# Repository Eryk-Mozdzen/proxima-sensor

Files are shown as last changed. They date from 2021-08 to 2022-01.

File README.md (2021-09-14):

# "Proxima" sensor

Simple, low cost, IR proximity sensor, designed for minisumo class robots. Operates at 56 kHz frequency. Dimensions: 12x17x15 mm.

## Projects goals
- \>20cm detection range
- 3.3/5V power supply voltage
- \<100mA power supply current
- single logic output
- smallest possible dimensions
- not operating at 38 kHz ([robot start module](https://p1r.se/startmodule/) frequency)
- plastic case
- status led

## Workflow

### Done:
- version 1.0 assembly
- raw tests
- replace resistors to compensate parasitic capacity
- tests with case

### In progress:
- searching for new square wave generator (NE555 is not suitable for aplications below 4.5V, but works)
- design better case 
	* receiver closer to front
	* add wall between receiver and transmitter led
	* add gap to improve taking out elektronics
	* increase hole diameter

### To do:
- print & test improved case

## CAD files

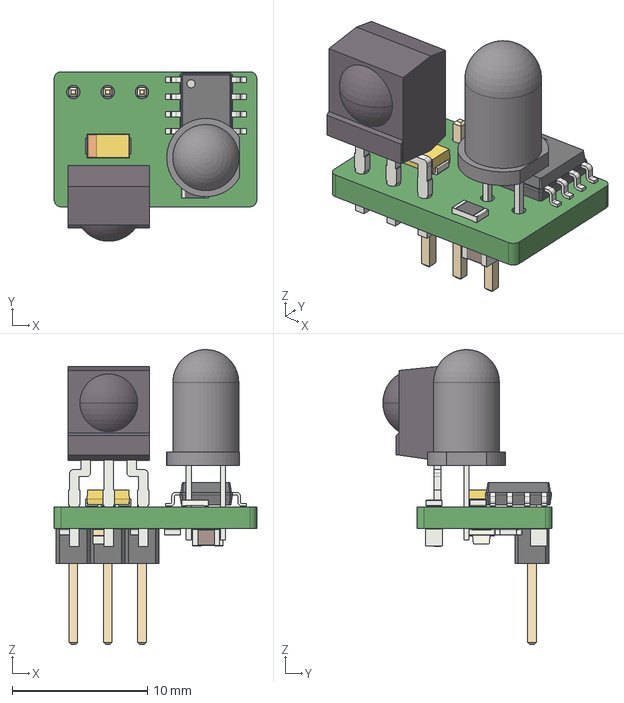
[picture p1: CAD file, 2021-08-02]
version_1.xx/proxima_sensor_case/exported_from_kicad/proxima_sensor_board.step
15.0 x 12.5 x 21.8 mm

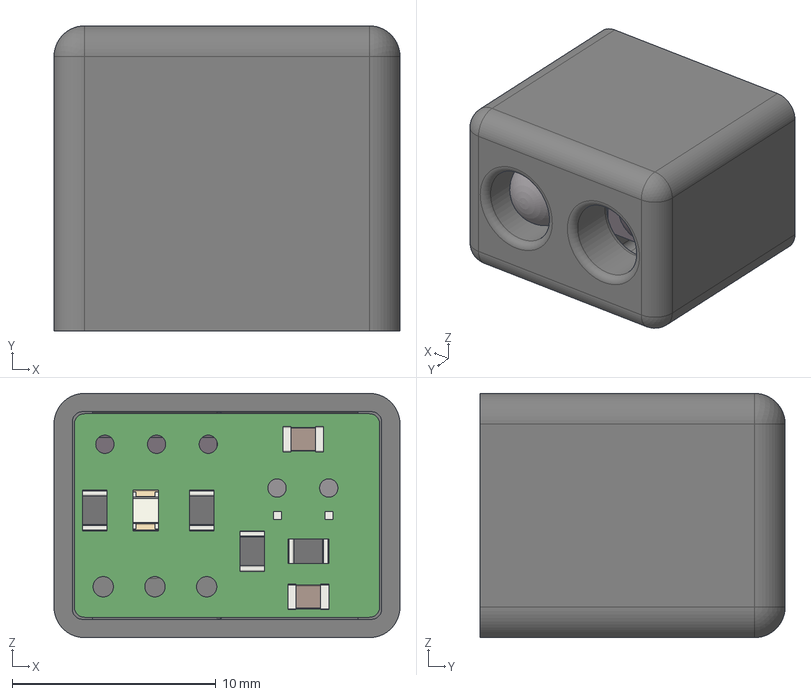
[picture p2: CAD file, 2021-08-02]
version_1.xx/proxima_sensor_case/proxima_sensor_model.stp
17.0 x 15.0 x 12.0 mm
proxima_case
proxima_kicadSOLID_1
proxima_kicadSOLID_2
proxima_kicadSOLID_3
proxima_kicadSOLID_4 x 5
proxima_kicadSOLID_5
proxima_kicadSOLID_6
proxima_kicadSOLID_7 x 2
proxima_kicadCOMPOUND

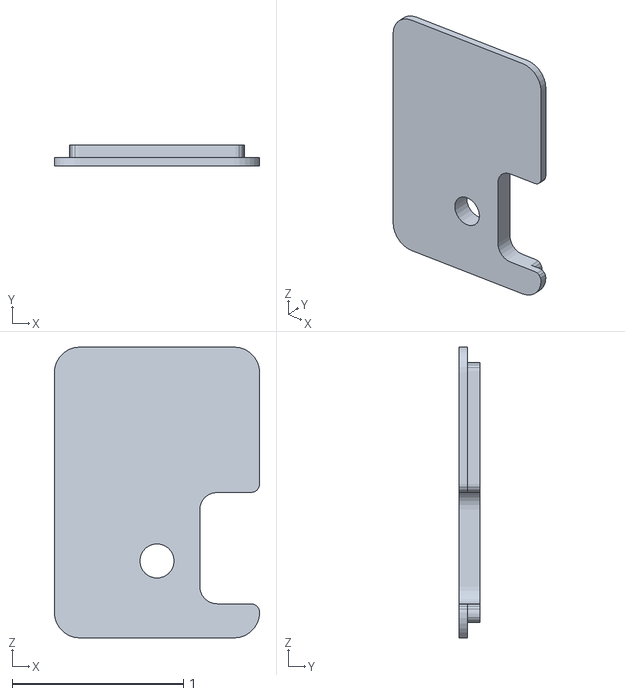
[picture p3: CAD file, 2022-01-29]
version_1.xx/proxima_sensor_case/stl_files/proxima_cup.stl
1.20 x 0.125 x 1.70

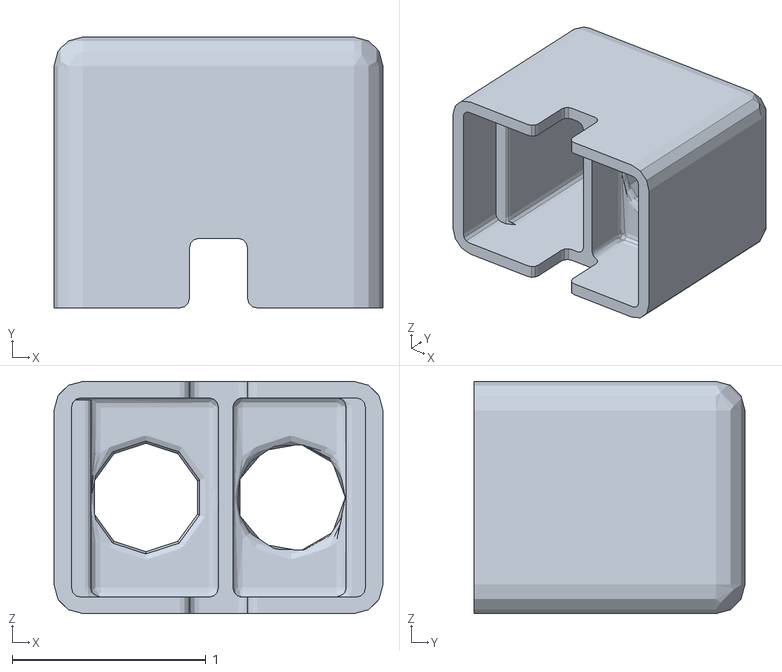
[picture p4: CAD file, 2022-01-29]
version_1.xx/proxima_sensor_case/stl_files/proxima_case.stl
1.70 x 1.40 x 1.20

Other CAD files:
version_1.xx/proxima_sensor_case/exported_from_kicad/OldVersions/proxima_kicadproxima_sensor_board.0009.iam
version_1.xx/proxima_sensor_case/exported_from_kicad/proxima_kicadCOMPOUND.ipt
version_1.xx/proxima_sensor_case/exported_from_kicad/proxima_kicadCP_EIA-3216-10_Kemet-I.iam
version_1.xx/proxima_sensor_case/exported_from_kicad/proxima_kicadC_0805_2012Metric.iam
version_1.xx/proxima_sensor_case/exported_from_kicad/proxima_kicadLED_0805_2012Metric.iam
version_1.xx/proxima_sensor_case/exported_from_kicad/proxima_kicadLED_D5.0mm_IRGrey.iam
version_1.xx/proxima_sensor_case/exported_from_kicad/proxima_kicadPinHeader_1x03_P2.54mm_Vertical.iam
version_1.xx/proxima_sensor_case/exported_from_kicad/proxima_kicadR_0805_2012Metric.iam
version_1.xx/proxima_sensor_case/exported_from_kicad/proxima_kicadSOIC-8_3.9x4.9mm_P1.27mm.iam
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

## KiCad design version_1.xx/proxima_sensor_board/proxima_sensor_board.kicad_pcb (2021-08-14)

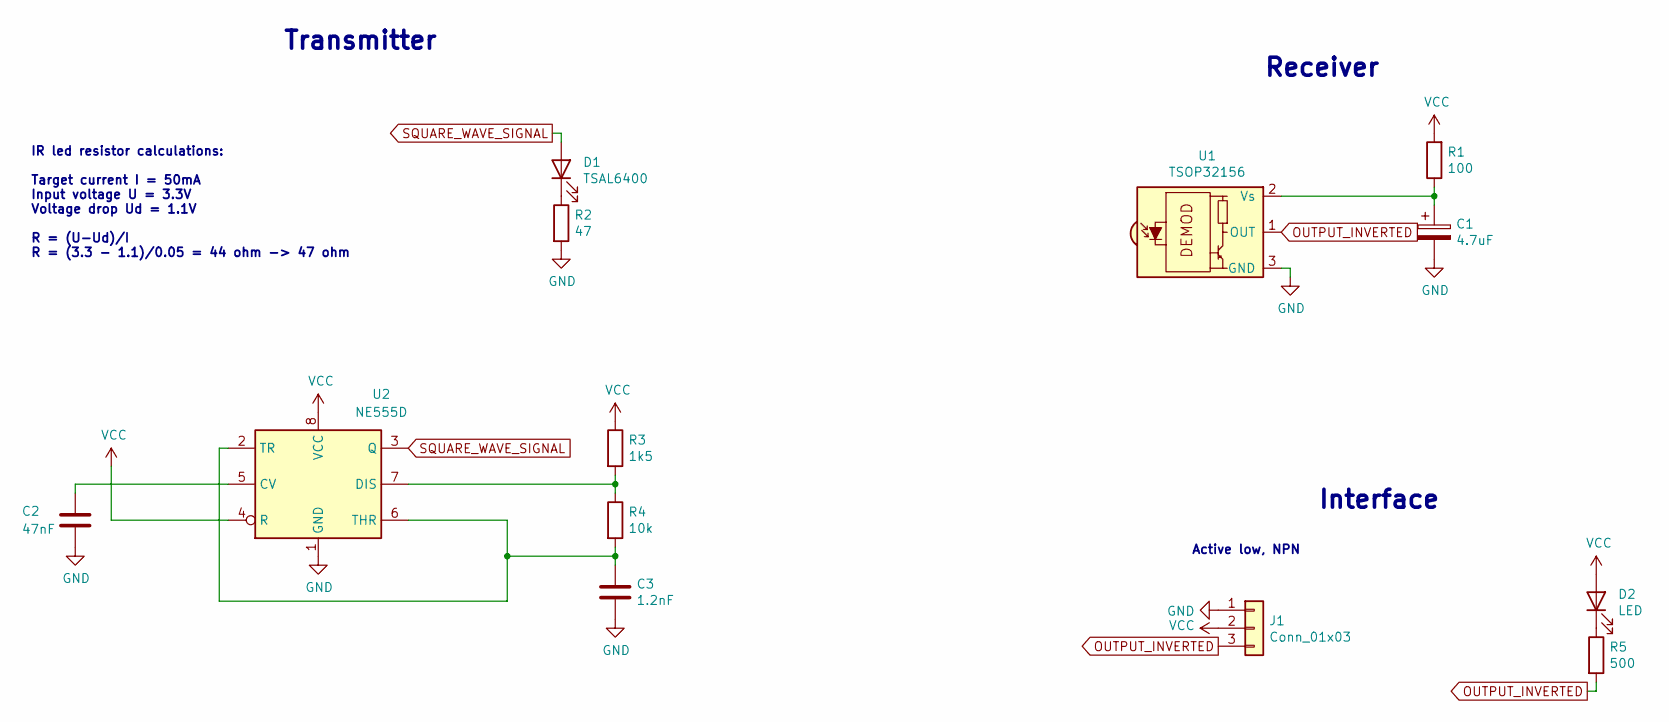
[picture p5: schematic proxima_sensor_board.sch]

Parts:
C1: 4.7uF; CP_EIA-3216-18_Kemet-A
C2: 47nF; C_0805_2012Metric
C3: 1.2nF; C_0805_2012Metric
D1: TSAL6400; LED_D5.0mm_IRGrey
D2: LED; LED_0805_2012Metric
J1: Conn_01x03; PinHeader_1x03_P2.54mm_Vertical
R1: 100; R_0805_2012Metric
R2: 47; R_0805_2012Metric
R3: 1k5; R_0805_2012Metric
R4: 10k; R_0805_2012Metric
R5: 500; R_0805_2012Metric
U1: TSOP32156; Vishay_MOLD-3Pin
U2: NE555D; SOIC-8_3.9x4.9mm_P1.27mm

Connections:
GND: C1.2, C2.2, C3.2, J1.1, R2.2, U1.3 (GND), U2.1 (GND)
unnamed: C1.1, R1.1, U1.2 (Vs)
unnamed: C2.1, U2.5 (CV)
unnamed: C3.1, R4.2, U2.2 (TR), U2.6 (THR)
unnamed: D1.1 (K), R2.1
unnamed: D2.1 (K), R5.1
unnamed: R3.2, R4.1, U2.7 (DIS)
OUTPUT_INVERTED: J1.3, R5.2, U1.1 (OUT)
SQUARE_WAVE_SIGNAL: D1.2 (A), U2.3 (Q)
VCC: D2.2 (A), J1.2, R1.2, R3.1, U2.4 (R), U2.8 (VCC)

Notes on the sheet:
IR led resistor calculations: Target current I = 50mA Input voltage U = 3.3V Voltage drop Ud = 1.1V R = (U-Ud)/I R = (3.3 - 1.1)/0.05 = 44 ohm -> 47 ohm
Transmitter
Receiver
Interface
Active low, NPN

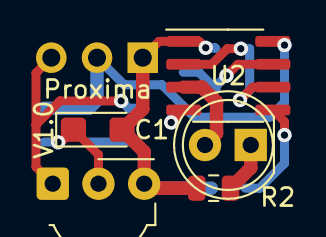
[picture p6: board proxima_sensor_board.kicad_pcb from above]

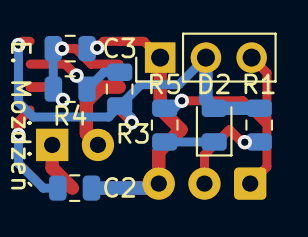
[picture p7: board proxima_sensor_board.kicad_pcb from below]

Board: 2 copper layers, 13 parts (8 on the bottom side), 10 nets.

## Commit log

2021-07-29 First schematic
    [proxima_sensor_board.kicad_pcb, proxima_sensor_board.sch]
2021-08-02 Smaller connector and version number
    [proxima_sensor_board.kicad_pcb, proxima_sensor_board.sch]
2021-08-02 Routes ready
    [proxima_sensor_board.kicad_pcb]
2021-08-02 Create 3D model
    [proxima_case.0020.ipt, proxima_case.ipt, proxima_kicadCOMPOUND.ipt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]
2021-08-02 Little fillet
    [proxima_V1.0.0001.ipt, proxima_case.0020.ipt, proxima_case.0021.ipt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]
2021-08-14 Panelize board and gerbers
    [proxima_panel-B_Cu.gbr, proxima_panel-B_Mask.gbr, proxima_panel-B_Paste.gbr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]
2021-08-15 Led calculations fix
    [proxima_sensor_board.sch]
2021-08-15 5mm breakway
    [proxima_panel-B_Cu.gbr, proxima_panel-B_Mask.gbr, proxima_panel-B_Paste.gbr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]
2021-08-16 panelization 2
    [proxima_panel-B_Cu.gbr, proxima_panel-B_Mask.gbr, proxima_panel-B_Paste.gbr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]
2021-09-13 First tests
    [proxima_case.stl, proxima_sensor_board.sch]
2021-09-14 Case improvements
    [proxima_V1.0.0001.ipt, proxima_case.0021.ipt, proxima_case.ipt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]
2022-01-19 update stl files
    [proxima_case.stl]
2022-01-29 update case
    [proxima_case.ipt, proxima_case.stl, proxima_cup.ipt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]
